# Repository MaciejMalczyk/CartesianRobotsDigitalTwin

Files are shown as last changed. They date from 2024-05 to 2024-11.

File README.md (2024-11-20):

# Cartesian Robots Digital Twin

Master's degree project. Functional pair of robots with digital twin made in FreeCAD. Repository consist all elements to build robots, program controllers and run software.

<p align="center">
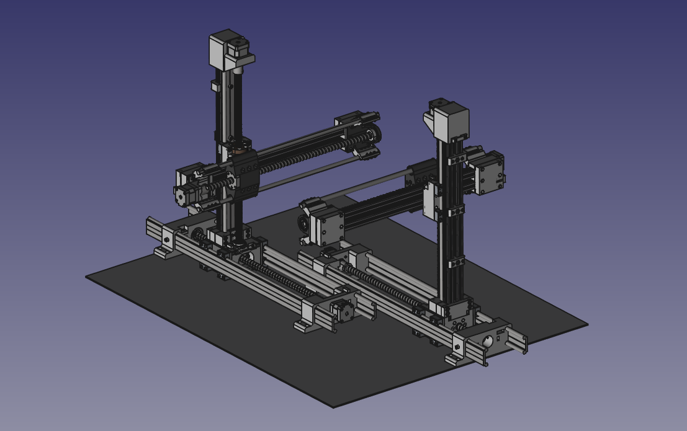
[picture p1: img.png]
    
</p>

## Contents

1. digitalTwin - FreeCAD project containing simplified models of robots with calculations,
2. documentation - 2D documentation of robots,
3. electronics - electronics schematic with designed board in KiCAD; used to connect motors with Arduino,
4. model - Autodesk Inventor model with .step export; additional FreeCAD designed t-slot nuts.
5. software - Arduino Uno code; FreeCAD macro for digitalTwin; misc - udev rules, examples; Qt ui.

## License

SOFTWARE: MIT
HARDWARE: CERN OHL v2, unless specified below

Igus® parts:
https://www.igus.eu/info/company-terms-and-conditions-de#section_15

Item® parts:
https://pl.item24.com/en/terms-and-conditions/

Autodesk Inventor Content Center files can have their own license.

## Acknowledgments

People involved in pre-alpha versions of CAD model: Wojciech Pyka, Maksymilian Jędrzejowski, Mateusz Chudy, Witold Krafczyk, Olaf Tokarczyk.

Maksymilian Jędrzejowski:
https://omega.polsl.pl/info/author/PSLde2ebd91c94b4b639f68adfb76bbbfe9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

Witold Krafczyk:
https://omega.polsl.pl/info/author/PSL3ab3095431ce463fbf17f6ad56f56e03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

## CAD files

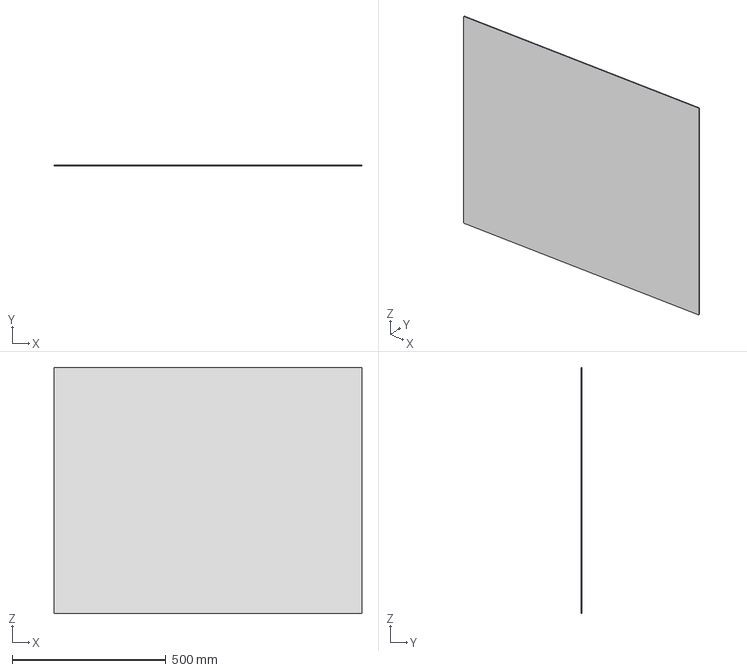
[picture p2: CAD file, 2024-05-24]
digitalTwin/aluminiumBase_ipt/0005.step
1000.0 x 3.00 x 800.0 mm

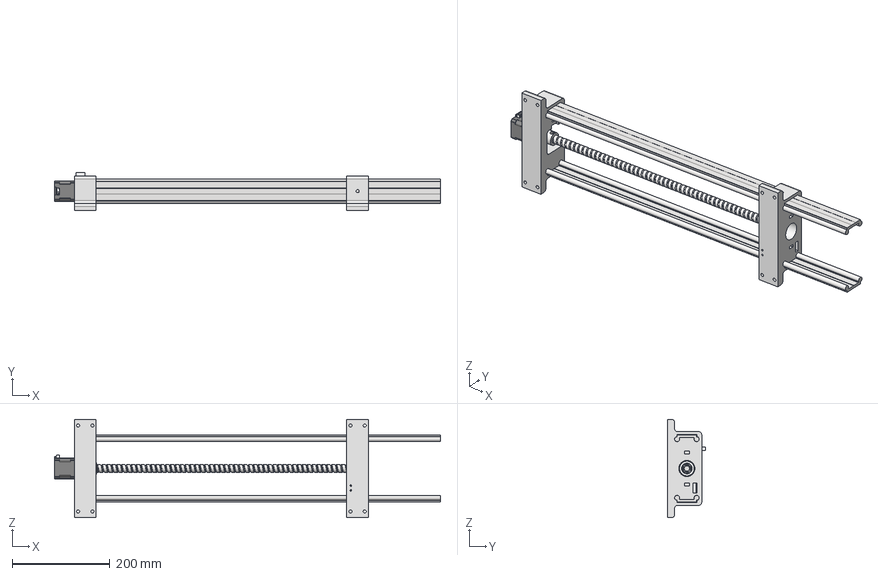
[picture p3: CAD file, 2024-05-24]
digitalTwin/X.stp
790.5 x 78.5 x 201.0 mm
Y_motor_mount
WS_10_40_X x 2
Y_motor_mount_1
Nema17 Stepper Motor
Cartesian1_BallScrew
Cartesian2_BallBearing_25x37x7
Cartesian1_12_12_Clutch
X_end_floating_cup
Connector_female
Stop_sw

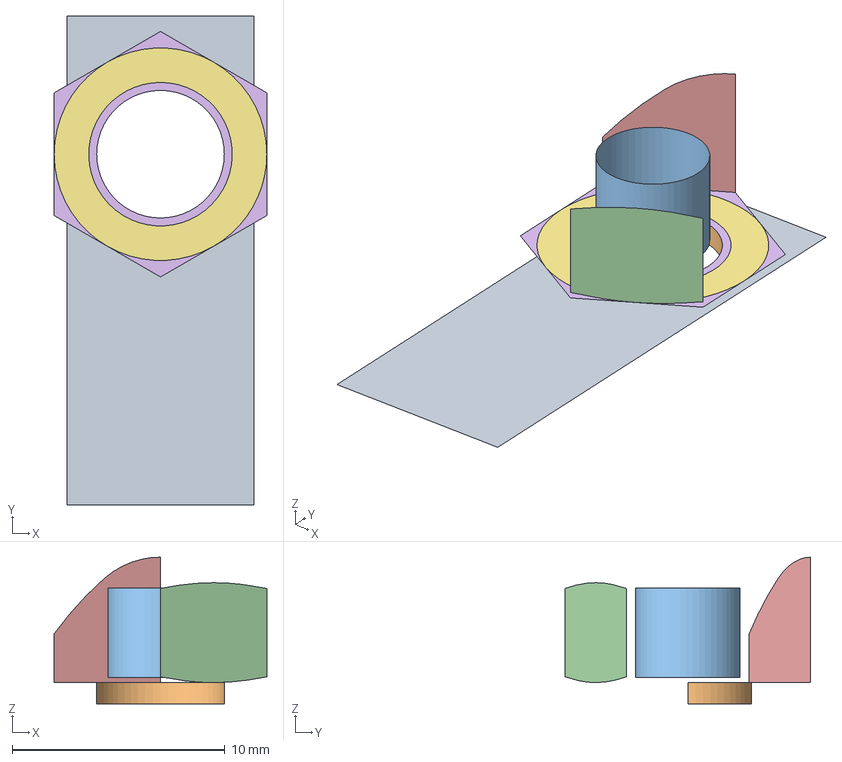
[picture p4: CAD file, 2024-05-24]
model/Additions/tslotNut8_M6.FCStd
10.0 x 23.0 x 6.90 mm
_Element
_Element001
_Element002
_Element003
_Element004
_Element005
_Element006

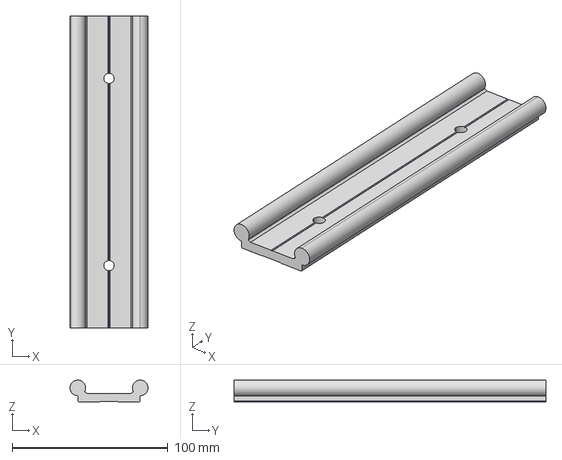
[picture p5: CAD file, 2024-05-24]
model/Workspaces/Obszar roboczy/content/igus/WS_10_40_200_1.stp
50.0 x 200.0 x 14.0 mm

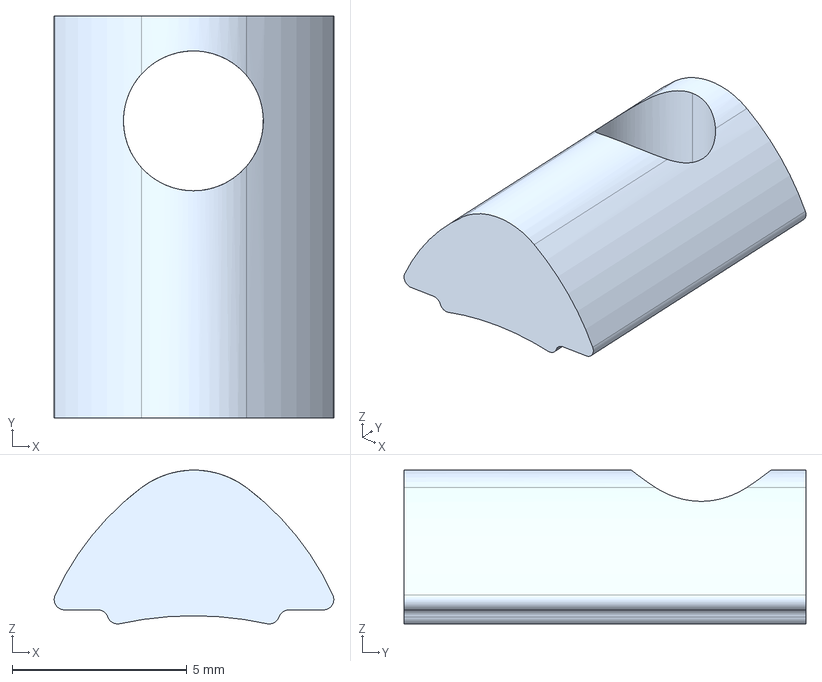
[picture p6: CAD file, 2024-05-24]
model/Workspaces/Obszar roboczy/content/item/item_0037006_Wpust_przesuwny_5_St_M4_1.stp
8.00 x 11.5 x 4.40 mm

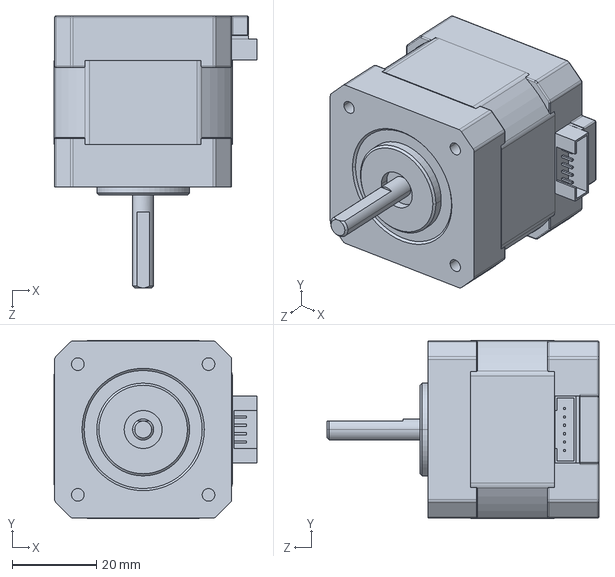
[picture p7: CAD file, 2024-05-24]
model/Workspaces/Obszar roboczy/content/nema17/17HS4401.STEP
48.2 x 42.3 x 64.5 mm

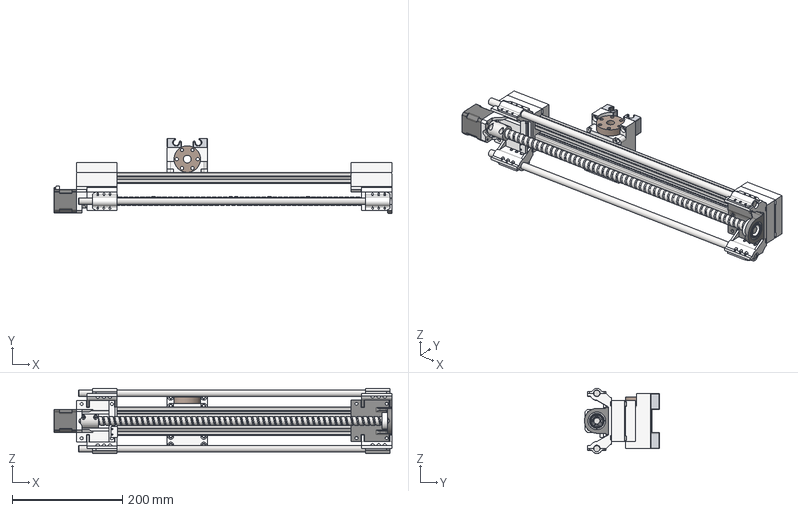
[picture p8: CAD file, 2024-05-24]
digitalTwin/Y.stp
612.5 x 136.2 x 118.5 mm
ZY_mount x 2
ZY_rod_mount x 2
motormount
Z_endstop_mount
Stop_sw
Z_bearingmount
item_0037003_Profile_5_20x20_L=564_1 x 2
Cartesian1_12mm_Rod x 2
Cartesian2_BallBearing_25x37x7
Cartesian1_X_RodCover x 4
Nema17 Stepper Motor
Cartesian1_12_12_Clutch
Cartesian1_BallScrew
Y_end_cover
Z_carriage
Cartesian1_Z_TrapezoiadlNut
WJ200UM_01_10_1 x 4
XItemEndCoverConnector
X_end_floating_cup

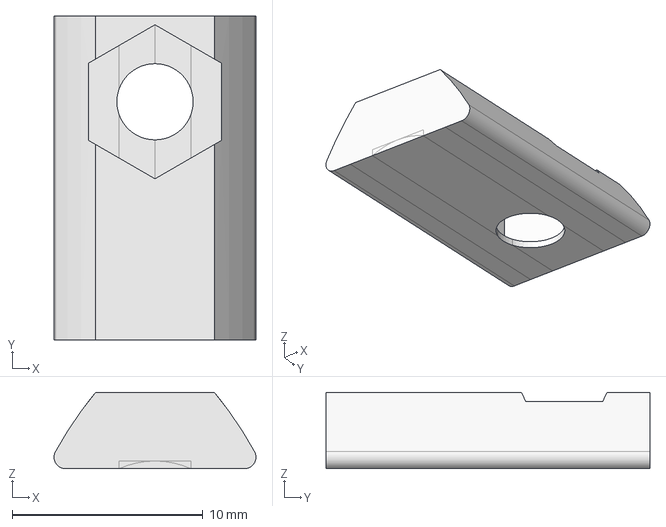
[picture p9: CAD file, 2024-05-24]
model/Additions/tslotNut6_M4.FCStd
10.6 x 17.0 x 4.00 mm

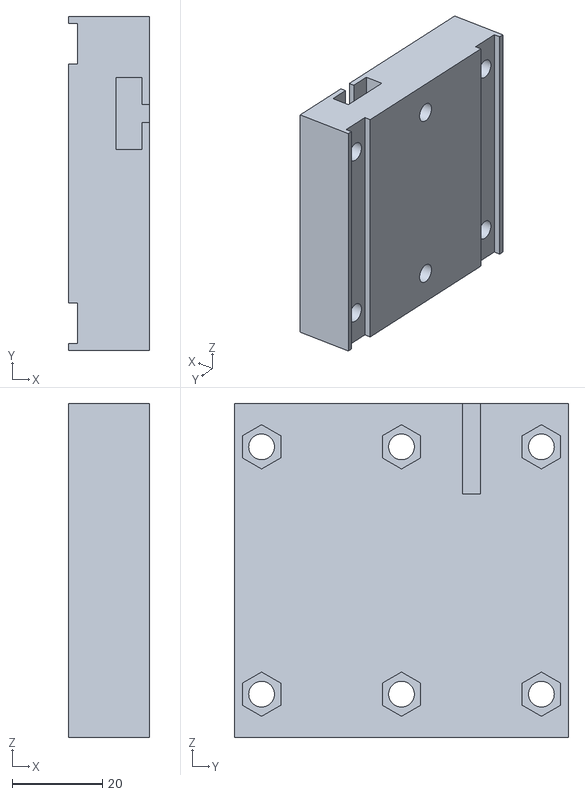
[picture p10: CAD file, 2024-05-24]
model/Workspaces/Obszar roboczy/assembly_v3/X/XItemEndCoverConnector.stl
18.0 x 74.0 x 74.0

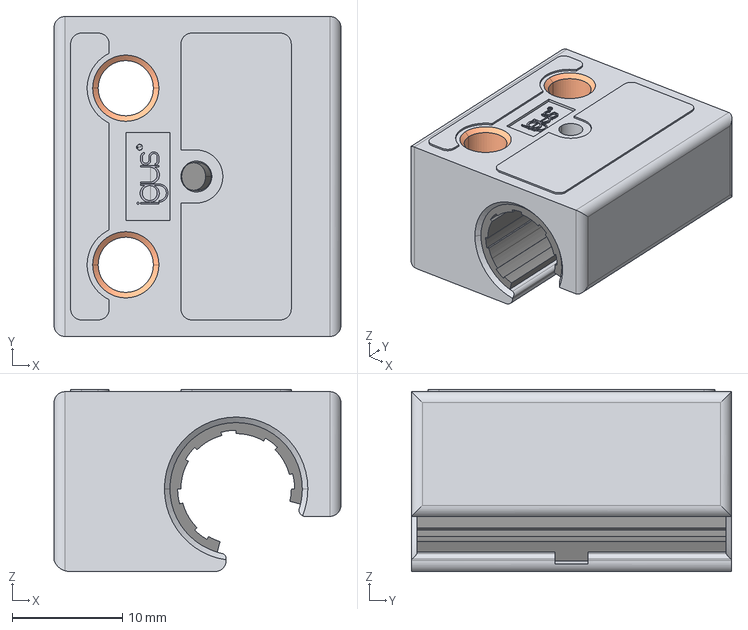
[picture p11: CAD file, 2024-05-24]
model/Workspaces/Obszar roboczy/content/igus/WJ200UM_01_10_1.stp
26.0 x 29.0 x 16.5 mm

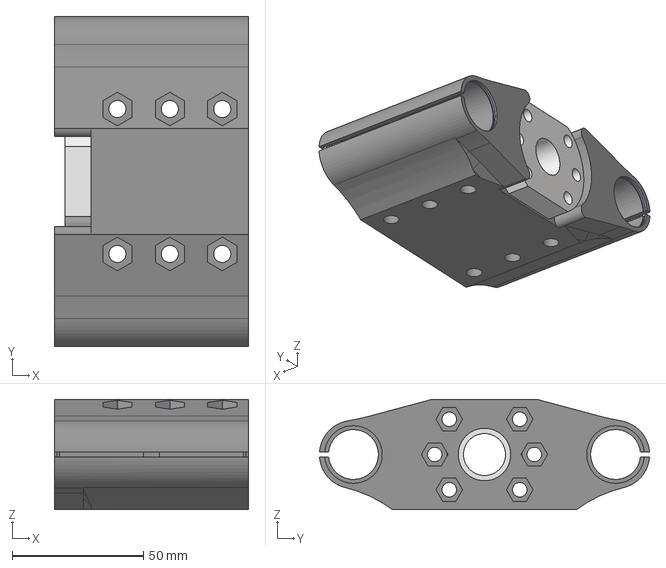
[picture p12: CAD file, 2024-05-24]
digitalTwin/C.stp
74.0 x 125.9 x 42.0 mm
Cartesian1_XYCarriage
Cartesian1_BallNut

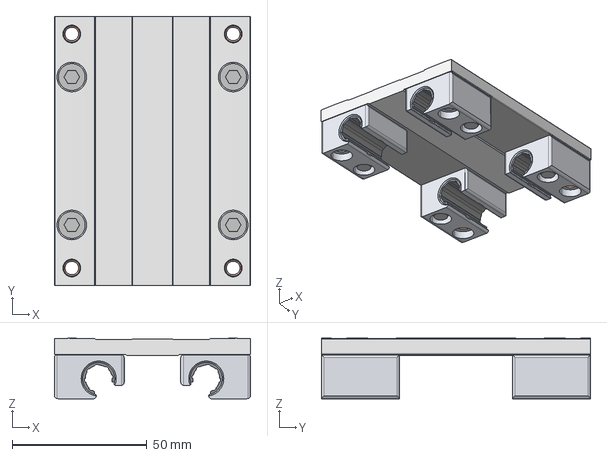
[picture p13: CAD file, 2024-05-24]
model/Workspaces/Obszar roboczy/content/igus/WW_10_40_10_2.stp
73.0 x 100.0 x 22.5 mm

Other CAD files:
model/Workspaces/Obszar roboczy/assembly_v3/Assembly.dwg
model/Workspaces/Obszar roboczy/assembly_v3/X/X.dwg
model/Workspaces/Obszar roboczy/assembly_v3/Y/Y.dwg
model/Workspaces/Obszar roboczy/assembly_v3/Z/Z.dwg
model/Workspaces/Obszar roboczy/content/igus/WS_10_80_200_1_FRONT.dwg
model/Workspaces/Obszar roboczy/assembly_v3/OldVersions/Assembly.0012.dwg
digitalTwin/aluminiumBase.ipt
model/Workspaces/Obszar roboczy/CC/pl-PL/ANSI B18.16.3M(2)/ANSI B18.16.3M - Klasa właściwości 5 i 10 - Metryczny M3 x 0.5 Typ metalowy.ipt
model/Workspaces/Obszar roboczy/CC/pl-PL/DIN 125-1 A/DIN 125 - A 3,2.ipt
model/Workspaces/Obszar roboczy/CC/pl-PL/DIN 472(1)/DIN 472 - 28 x 1,2.ipt
model/Workspaces/Obszar roboczy/CC/pl-PL/DIN 7984/DIN 7984 - M3 x 14.ipt
model/Workspaces/Obszar roboczy/CC/pl-PL/DIN 7984/DIN 7984 - M3 x 18.ipt
model/Workspaces/Obszar roboczy/CC/pl-PL/DIN 7984/DIN 7984 - M4 x 14.ipt
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

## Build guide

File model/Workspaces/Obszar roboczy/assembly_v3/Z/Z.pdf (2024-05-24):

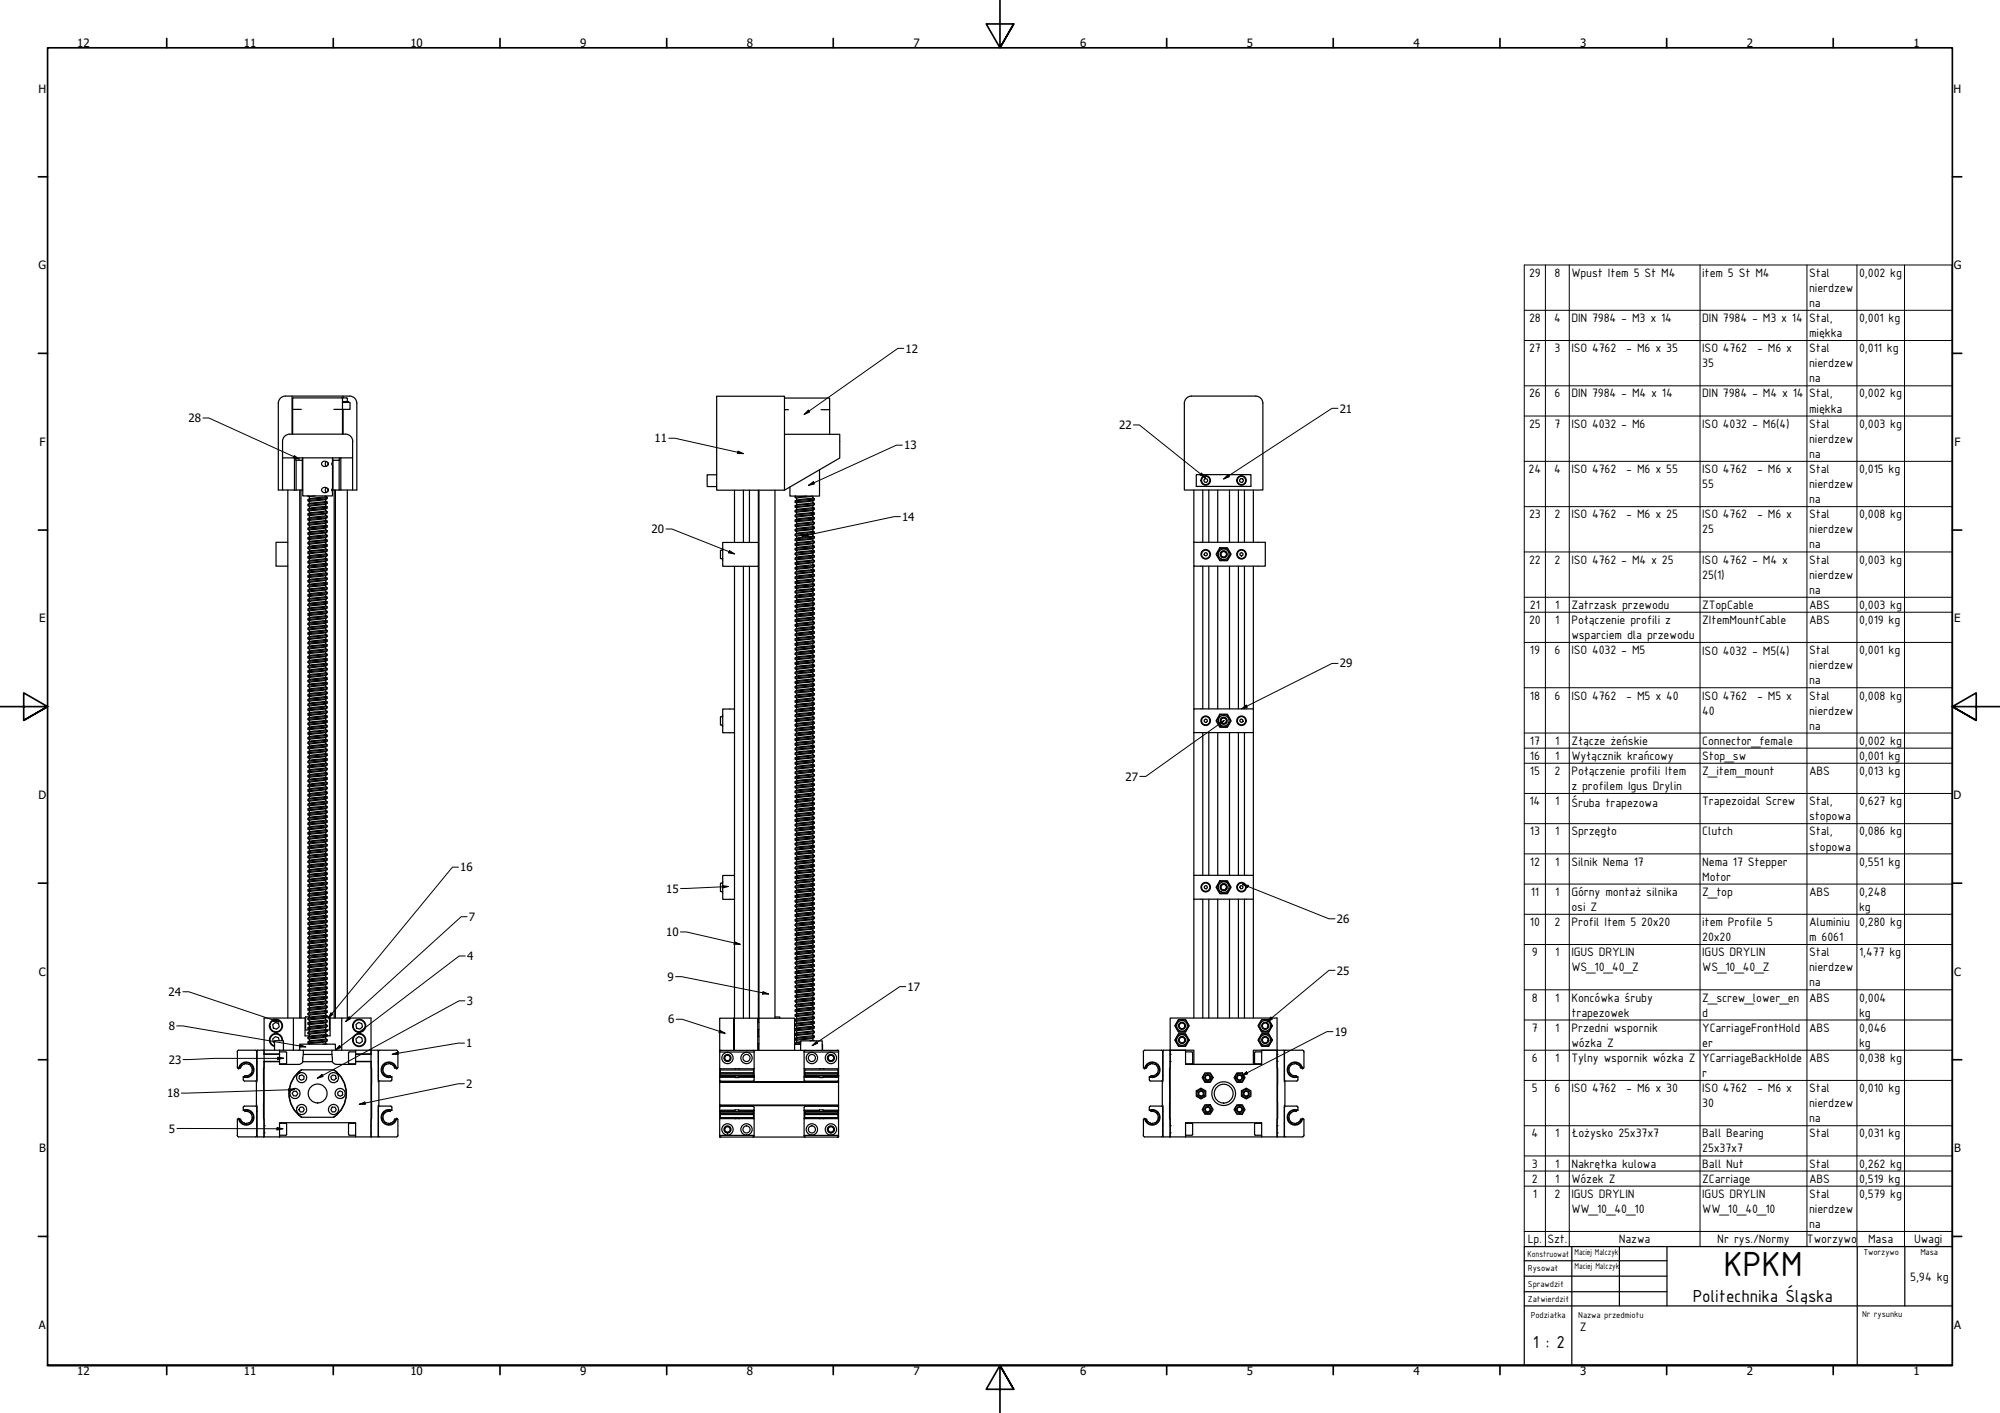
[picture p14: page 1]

2 9 | 8 | W p u s t It e m 5 S t M 4 | it e m 5 S t M 4 | S t a l nie r d z e w n a | 0,0 0 2 k g

2 8 | 4 | DIN 7 9 8 4 -M 3 x 1 4 | DIN 7 9 8 4 -M 3 x 1 4 | S t a l, mi k k a | 0,0 0 1 k g

2 7 | 3 | IS O 4 7 6 2 -M 6 x 3 5 | | S a ISO 4762 - M6 x 35 t a l nie r d z e w n | 0,0 1 1 k g

2 6 | 6 | DIN 7 9 8 4 -M 4 x 1 4 | DIN 7 9 8 4 -M 4 x 1 4 | S t a l, mi k k a | 0,0 0 2 k g

2 5 | 7 | IS O 4 0 3 2 -M 6 | ( ) IS O 4 0 3 2 -M 6 4 | S t a l nie r d z e w n a | 0,0 0 3 k g

2 4 | 4 | IS O 4 7 6 2 -M 6 x 5 5 | | S a ISO 4762 - M6 x 55 t a l nie r d z e w n | 0,0 1 5 k g

2 3 | 2 | IS O 4 7 6 2 -M 6 x 2 5 | | S a ISO 4762 - M6 x 25 t a l nie r d z e w n | 0,0 0 8 k g

2 2 | 2 | IS O 4 7 6 2 -M 4 x 2 5 | | S a ISO 4762 - M4 x 25(1) t a l nie r d z e w n | 0,0 0 3 k g

2 1 | 1 | Z a t r z a s k p r z e w o d u | Z T o p C a b l e | A B S | 0,0 0 3 k g
2 0 | 1 |  P o ò c z e nie p r o fili z w s p a r cie m d l a p r z e w o d u | ZIt e m M o u n t C a b l e | A B S | 0,0 1 9 k g

1 9 | 6 | IS O 4 0 3 2 -M 5 | ( ) IS O 4 0 3 2 -M 5 4 | S t a l nie r d z e w n a | 0,0 0 1 k g

1 8 | 6 | IS O 4 7 6 2 -M 5 x 4 0 | | S a ISO 4762 - M5 x 40 t a l nie r d z e w n | 0,0 0 8 k g

1 7 | 1 |  Z  ò c z e  e s kie | C o n n e c t o r_f e m a l e | | 0,0 0 2 k g
1 6 | 1 |  W y  ò c z nik k r a c o w y | S t o p_s w | | 0,0 0 1 k g
1 5 | 2 |  P o ò c z e nie p r o fili It e m z p r o fil e m Ig u s D r y lin | Z_it e m_m o u n t | A B S | 0,0 1 3 k g

1 4 | 1 |  r u b a t r a p e z o w a | T r a p e z oid a l S c r e w | S t a l, s t o p o w a | 0,6 2 7 k g

1 2 | 1 | Sil nik N e m a 1 7 | N e m a 1 7 S t e p p e r M o t o r | | 0,5 5 1 k g

1 1 | 1 | ¦ G r n y m o n t a  sil nik a o si Z | Z_t o p | A B S | 0,2 4 8 k g

1 0 | 2 | P r o fil It e m 5 2 0 x 2 0 | | A l u miniu 1 item Profile 5 20x20 m 6 0 6 | 0,2 8 0 k g

9 | 1 | | | S a IGUS DRYLIN WS_10_40_Z IGUS DRYLIN WS_10_40_Z t a l nie r d z e w n | 1,4 7 7 k g

7 | 1 | P r z e d ni w s p o r nik w ¦ z k a Z | Y C a r ria g e F r o n t H o l d e r | A B S | 0,0 4 6 k g

6 | 1 | ¦ T y l n y w s p o r nik w z k a Z | Y C a r ria g e B a c k H o l d e r | A B S | 0,0 3 8 k g

5 | 6 | IS O 4 7 6 2 -M 6 x 3 0 | | S a ISO 4762 - M6 x 30 t a l nie r d z e w n | 0,0 1 0 k g

4 | 1 |  o  y s k o 2 5 x 3 7 x 7 | B a l l B e a rin g 2 5 x 3 7 x 7 | S t a l | 0,0 3 1 k g

3 | 1 | N a k r  t k a k u l o w a | B a l l N u t | S t a l | 0,2 6 2 k g
2 | 1 | ¦ W z e k Z | Z C a r ria g e | A B S | 0,5 1 9 k g
1 | 2 | | | S a IGUS DRYLIN WW_10_40_10 IGUS DRYLIN WW_10_40_10 t a l nie r d z e w n | 0,5 7 9 k g
K o n s t r u o w a  | M a ciej M a l c z y k | | K P K M  P o lit e c h nik a l ò s k a | T w o r z y w o | M a s a 5,9 4 k g
 R y s o w a | M a ciej M a l c z y k

Z a t wie r d zi

P o d zia  k a 1 : 2 | N a z w a p r z e d mio t u Z | | | N r r y s u n k u

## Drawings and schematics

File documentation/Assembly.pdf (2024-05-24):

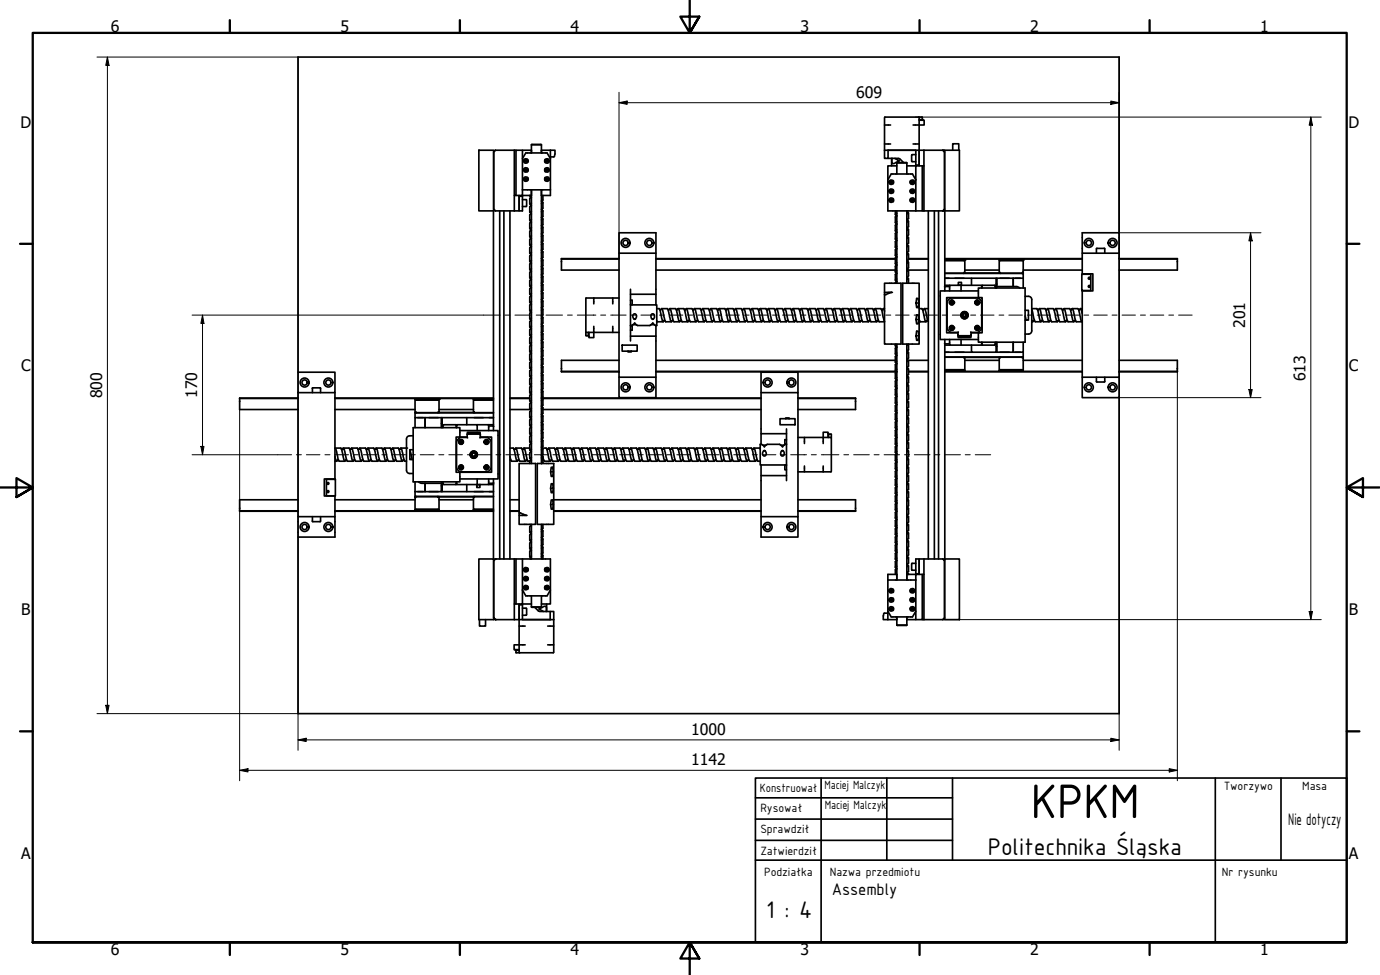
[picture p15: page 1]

Konstruowa | Maciej Malczyk | KPKM Politechnika lòska | Tworzywo | Masa Nie dotyczy
Rysowa | Maciej Malczyk
Zatwierdzi

Sprawdzi

Podziaka 1 : 4 | Nazwa przedmiotu Assembly | | Nr rysunku

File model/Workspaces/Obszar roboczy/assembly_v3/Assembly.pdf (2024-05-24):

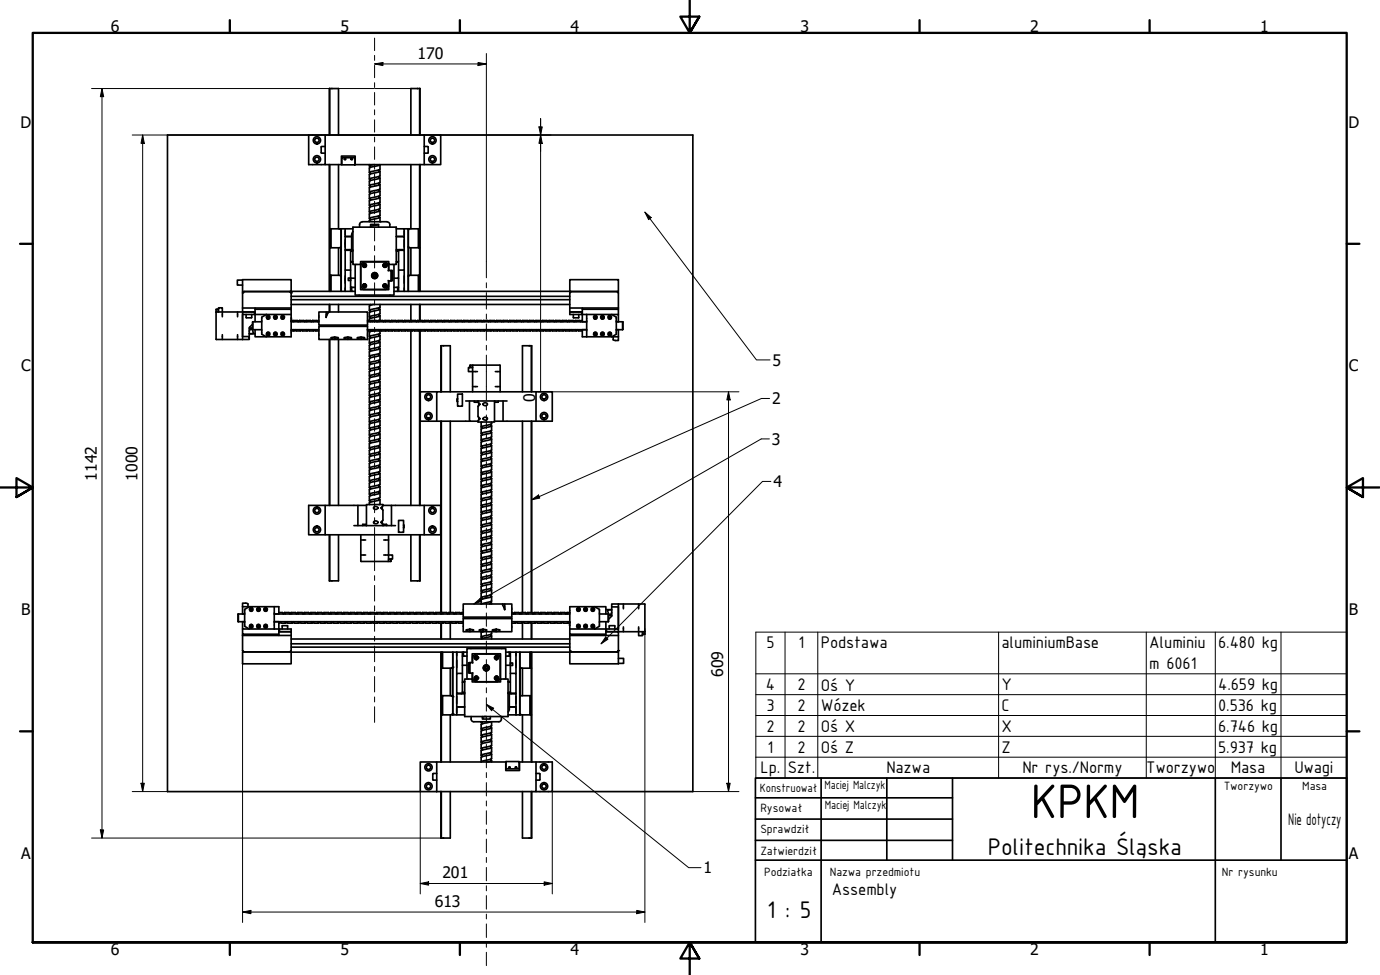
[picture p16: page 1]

5 | 1 | Podstawa | aluminiumBase | Aluminiu m 6061 | 6.480 kg

4 | 2 | O Y | Y | | 4.659 kg
3 | 2 | W¦zek | C | | 0.536 kg
2 | 2 | O X | X | | 6.746 kg
1 | 2 | O Z | Z | | 5.937 kg
Lp. | Szt. | Nazwa | Nr rys./Normy | Tworzywo | Masa | Uwagi
Konstruowa | Maciej Malczyk | | KPKM Politechnika lòska | Tworzywo | Masa Nie dotyczy
Rysowa | Maciej Malczyk
Zatwierdzi

Sprawdzi

Podziaka 1 : 5 | Nazwa przedmiotu Assembly | | | Nr rysunku

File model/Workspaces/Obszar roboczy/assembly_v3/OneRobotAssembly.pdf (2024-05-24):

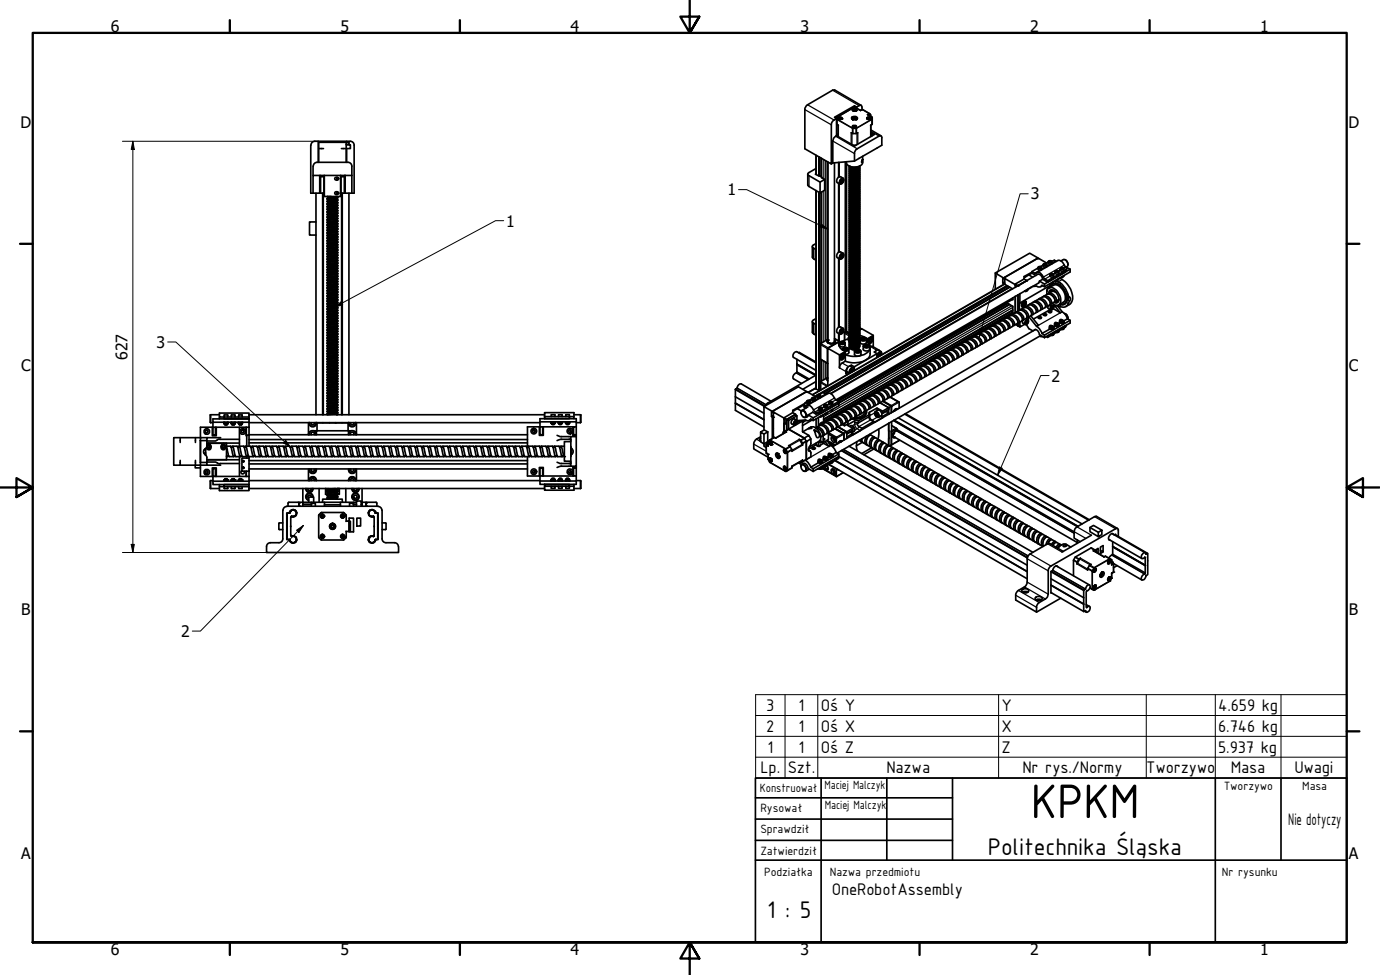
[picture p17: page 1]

3 | 1 | O Y | Y | | 4.659 kg
2 | 1 | O X | X | | 6.746 kg
1 | 1 | O Z | Z | | 5.937 kg
Lp. | Szt. | Nazwa | Nr rys./Normy | Tworzywo | Masa | Uwagi
Konstruowa | Maciej Malczyk | | KPKM Politechnika lòska | Tworzywo | Masa Nie dotyczy
Rysowa | Maciej Malczyk
Zatwierdzi

Sprawdzi

Podziaka 1 : 5 | Nazwa przedmiotu OneRobotAssembly | | | Nr rysunku

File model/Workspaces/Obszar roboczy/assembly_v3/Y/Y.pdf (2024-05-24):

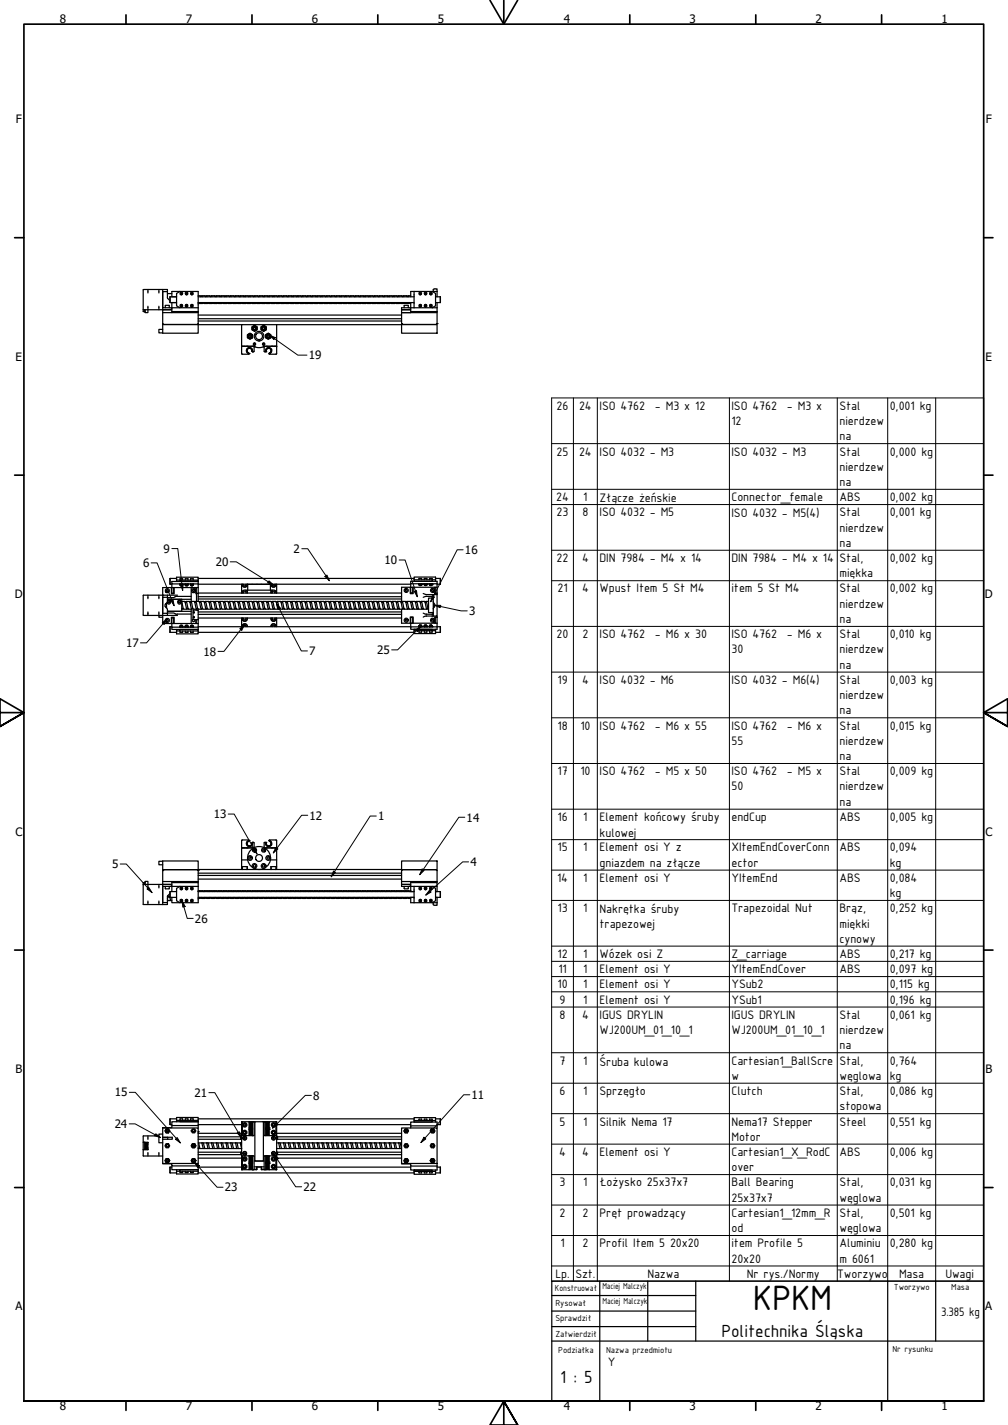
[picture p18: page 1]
Stal,; Ball Bearing

26 | 24 | ISO 4762 - M3 x 12 | ISO 4762 - M3 x 12 | Stal nierdzew na | 0,001 kg

25 | 24 | ISO 4032 - M3 | ISO 4032 - M3 | Stal nierdzew na | 0,000 kg

24 | 1 | Zòcze eskie | Connector_female | ABS | 0,002 kg
23 | 8 | ISO 4032 - M5 | ISO 4032 - M5(4) | Stal nierdzew na | 0,001 kg

22 | 4 | DIN 7984 - M4 x 14 | DIN 7984 - M4 x 14 | Stal, mikka | 0,002 kg

21 | 4 | Wpust Item 5 St M4 | item 5 St M4 | Stal nierdzew na | 0,002 kg

20 | 2 | ISO 4762 - M6 x 30 | ISO 4762 - M6 x 30 | Stal nierdzew na | 0,010 kg

19 | 4 | ISO 4032 - M6 | ISO 4032 - M6(4) | Stal nierdzew na | 0,003 kg

18 | 10 | ISO 4762 - M6 x 55 | ISO 4762 - M6 x 55 | Stal nierdzew na | 0,015 kg

17 | 10 | ISO 4762 - M5 x 50 | ISO 4762 - M5 x 50 | Stal nierdzew na | 0,009 kg

16 | 1 | Element kocowy ruby kulowej | endCup | ABS | 0,005 kg

15 | 1 | Element osi Y z gniazdem na zòcze | XItemEndCoverConn ector | ABS | 0,094 kg

14 | 1 | Element osi Y | YItemEnd | ABS | 0,084 kg

13 | 1 | Nakrtka ruby trapezowej | Trapezoidal Nut | Bròz, mikki cynowy | 0,252 kg

12 | 1 | W¦zek osi Z | Z_carriage | ABS | 0,217 kg
11 | 1 | Element osi Y | YItemEndCover | ABS | 0,097 kg
10 | 1 | Element osi Y | YSub2 | | 0,115 kg
9 | 1 | Element osi Y | YSub1 | | 0,196 kg
8 | 4 | IGUS DRYLIN WJ200UM_01_10_1 | IGUS DRYLIN WJ200UM_01_10_1 | Stal nierdzew na | 0,061 kg

7 | 1 | ruba kulowa | Cartesian1_BallScre w | Stal, wglowa | 0,764 kg

6 | 1 | Sprzgo | Clutch | Stal, stopowa | 0,086 kg

5 | 1 | Silnik Nema 17 | Nema17 Stepper Motor | Steel | 0,551 kg

4 | 4 | Element osi Y | Cartesian1_X_RodC over | ABS | 0,006 kg

2 | 2 | Prt prowadzòcy | Cartesian1_12mm_R od | Stal, wglowa | 0,501 kg

1 | 2 | Profil Item 5 20x20 | item Profile 5 20x20 | Aluminiu m 6061 | 0,280 kg
Konstruowa | Maciej Malczyk | | KPKM Politechnika lòska | Tworzywo | Masa 3.385 kg
Rysowa | Maciej Malczyk
Zatwierdzi

Lp. | Szt. | Nazwa | Nr rys./Normy | Tworzywo | Masa | Uwagi

Sprawdzi

Podziaka 1 : 5 | Nazwa przedmiotu Y | | | Nr rysunku

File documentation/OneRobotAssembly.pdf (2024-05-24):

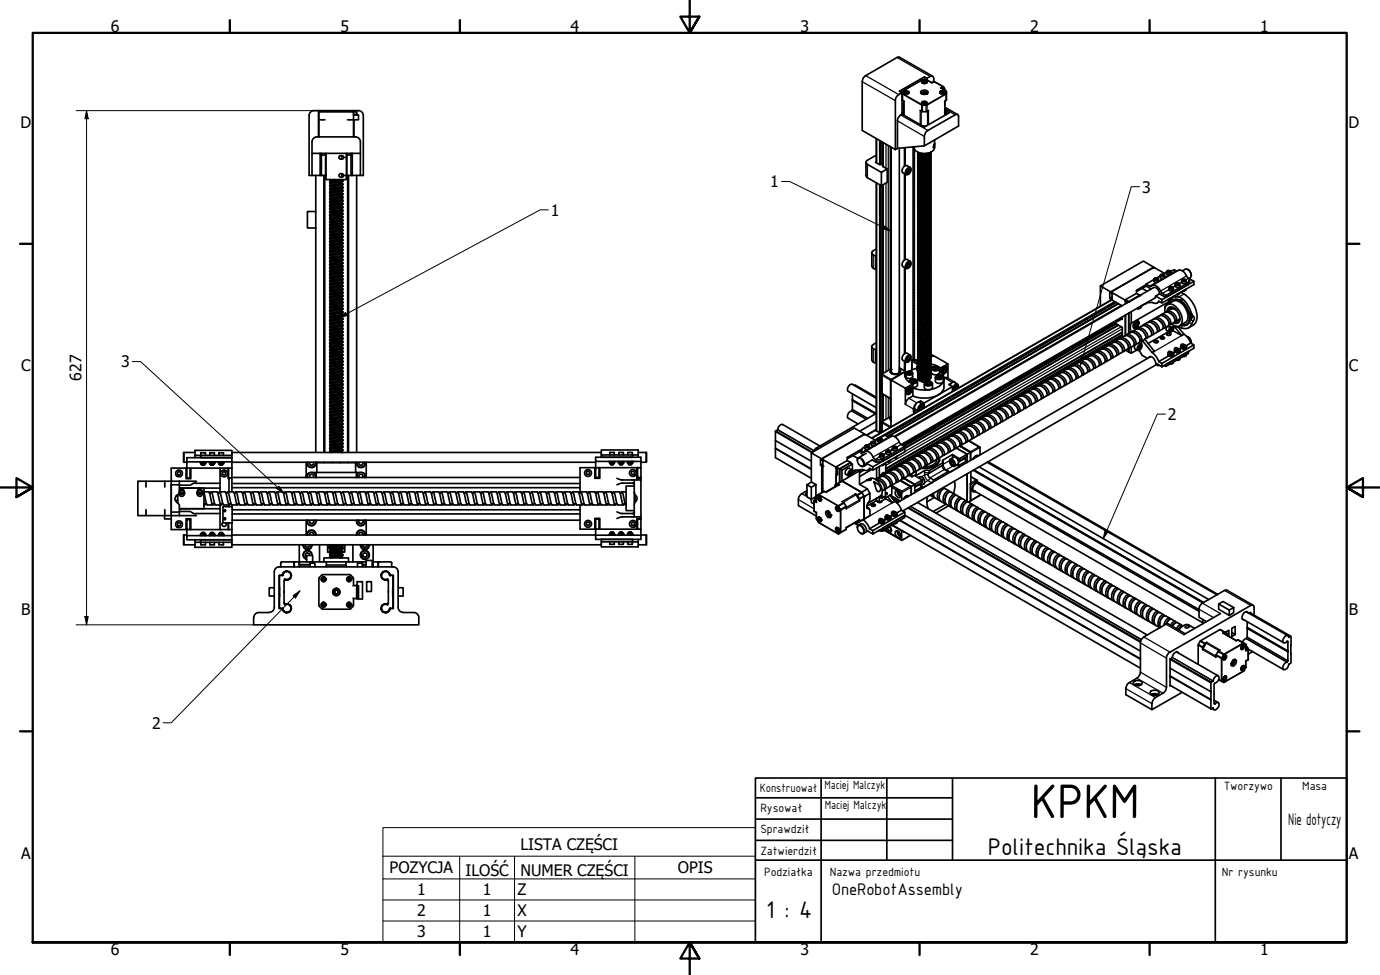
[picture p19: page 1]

Konstruowa | Maciej Malczyk | KPKM Politechnika lòska | Tworzywo | Masa Nie dotyczy
Rysowa | Maciej Malczyk
Zatwierdzi

Sprawdzi

LISTA CZCI

POZYCJA | ILOû | NUMER CZCI | OPIS

Podziaka 1 : 4 | Nazwa przedmiotu OneRobotAssembly | | Nr rysunku

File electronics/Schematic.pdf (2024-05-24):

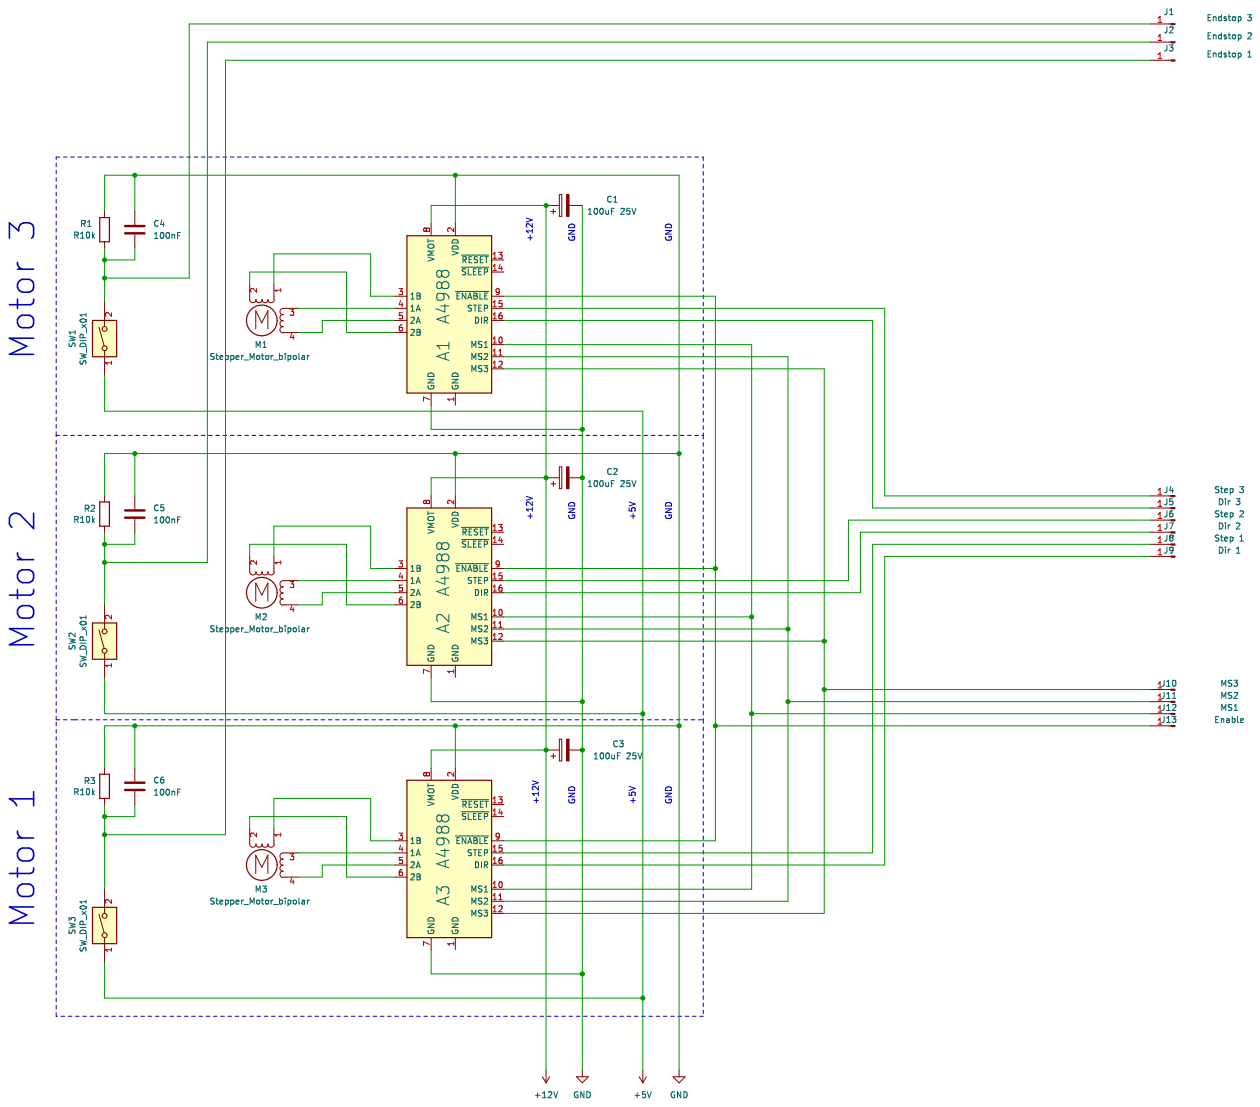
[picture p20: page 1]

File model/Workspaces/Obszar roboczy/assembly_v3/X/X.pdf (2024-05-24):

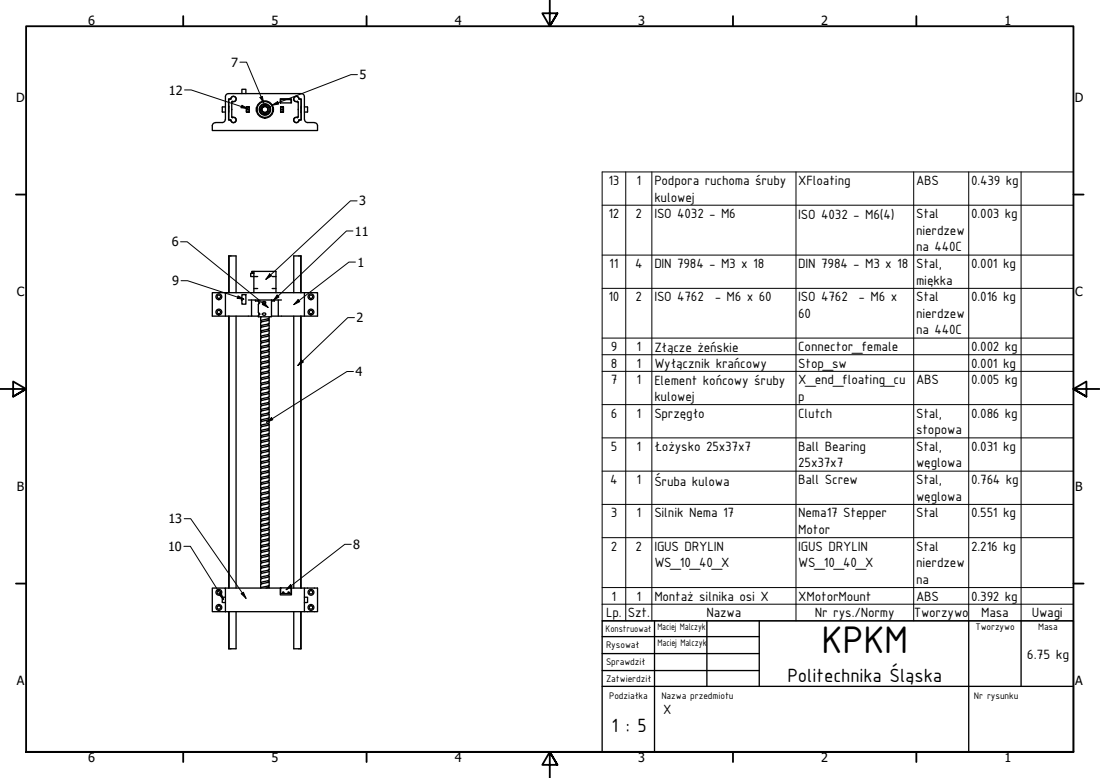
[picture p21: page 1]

1 3 | 1 | P o d p o r a r u c h o m a  r u b y k u l o w ej | X F l o a tin g | A B S | 0.4 3 9 k g

1 2 | 2 | IS O 4 0 3 2 -M 6 | IS O 4 0 3 2 -M 6 ( 4 ) | S t a l nie r d z e w n a 4 4 0 C | 0.0 0 3 k g

1 1 | 4 | DIN 7 9 8 4 -M 3 x 1 8 | DIN 7 9 8 4 -M 3 x 1 8 | S t a l, mi k k a | 0.0 0 1 k g

1 0 | 2 | IS O 4 7 6 2 -M 6 x 6 0 | | S t a l C ISO 4762 - M6 x 60 nie r d z e w n a 4 4 0 | 0.0 1 6 k g

9 | 1 | Z  ò c z e  e  s kie | C o n n e c t o r_f e m a l e | | 0.0 0 2 k g
8 | 1 | W y  ò c z nik k r a  c o w y | S t o p_s w | | 0.0 0 1 k g
7 | 1 | E l e m e n t k o  c o w y  r u b y k u l o w ej | X_e n d_f l o a tin g_c u p | A B S | 0.0 0 5 k g

5 | 1 |  o  y s k o 2 5 x 3 7 x 7 | B a l l B e a rin g 2 5 x 3 7 x 7 | S t a l, w  g l o w a | 0.0 3 1 k g

3 | 1 | Sil nik N e m a 1 7 | N e m a 1 7 S t e p p e r M o t o r | S t a l | 0.5 5 1 k g

2 | 2 | | | S a IGUS DRYLIN WS_10_40_X IGUS DRYLIN WS_10_40_X t a l nie r d z e w n | 2.2 1 6 k g

1 | 1 | M o n t a  sil nik a o si X | X M o t o r M o u n t | A B S | 0.3 9 2 k g
L p. S | z t. N | a z w a | N r r y s./ N o r m y | T w o r z y w o | M a s a | U w a
K o n s t r u o w a  | M a ciej M a l c z y k | | K P K M  P o lit e c h nik a l ò s k a | T w o r z y w o | M a s a 6.7 5 k g
R y s o w a  | M a ciej M a l c z y k

Z a t wie r d zi

P o d zia  k a 1 : 5 | N a z w a p r z e d mio t u X | | | N r r y s u n k u

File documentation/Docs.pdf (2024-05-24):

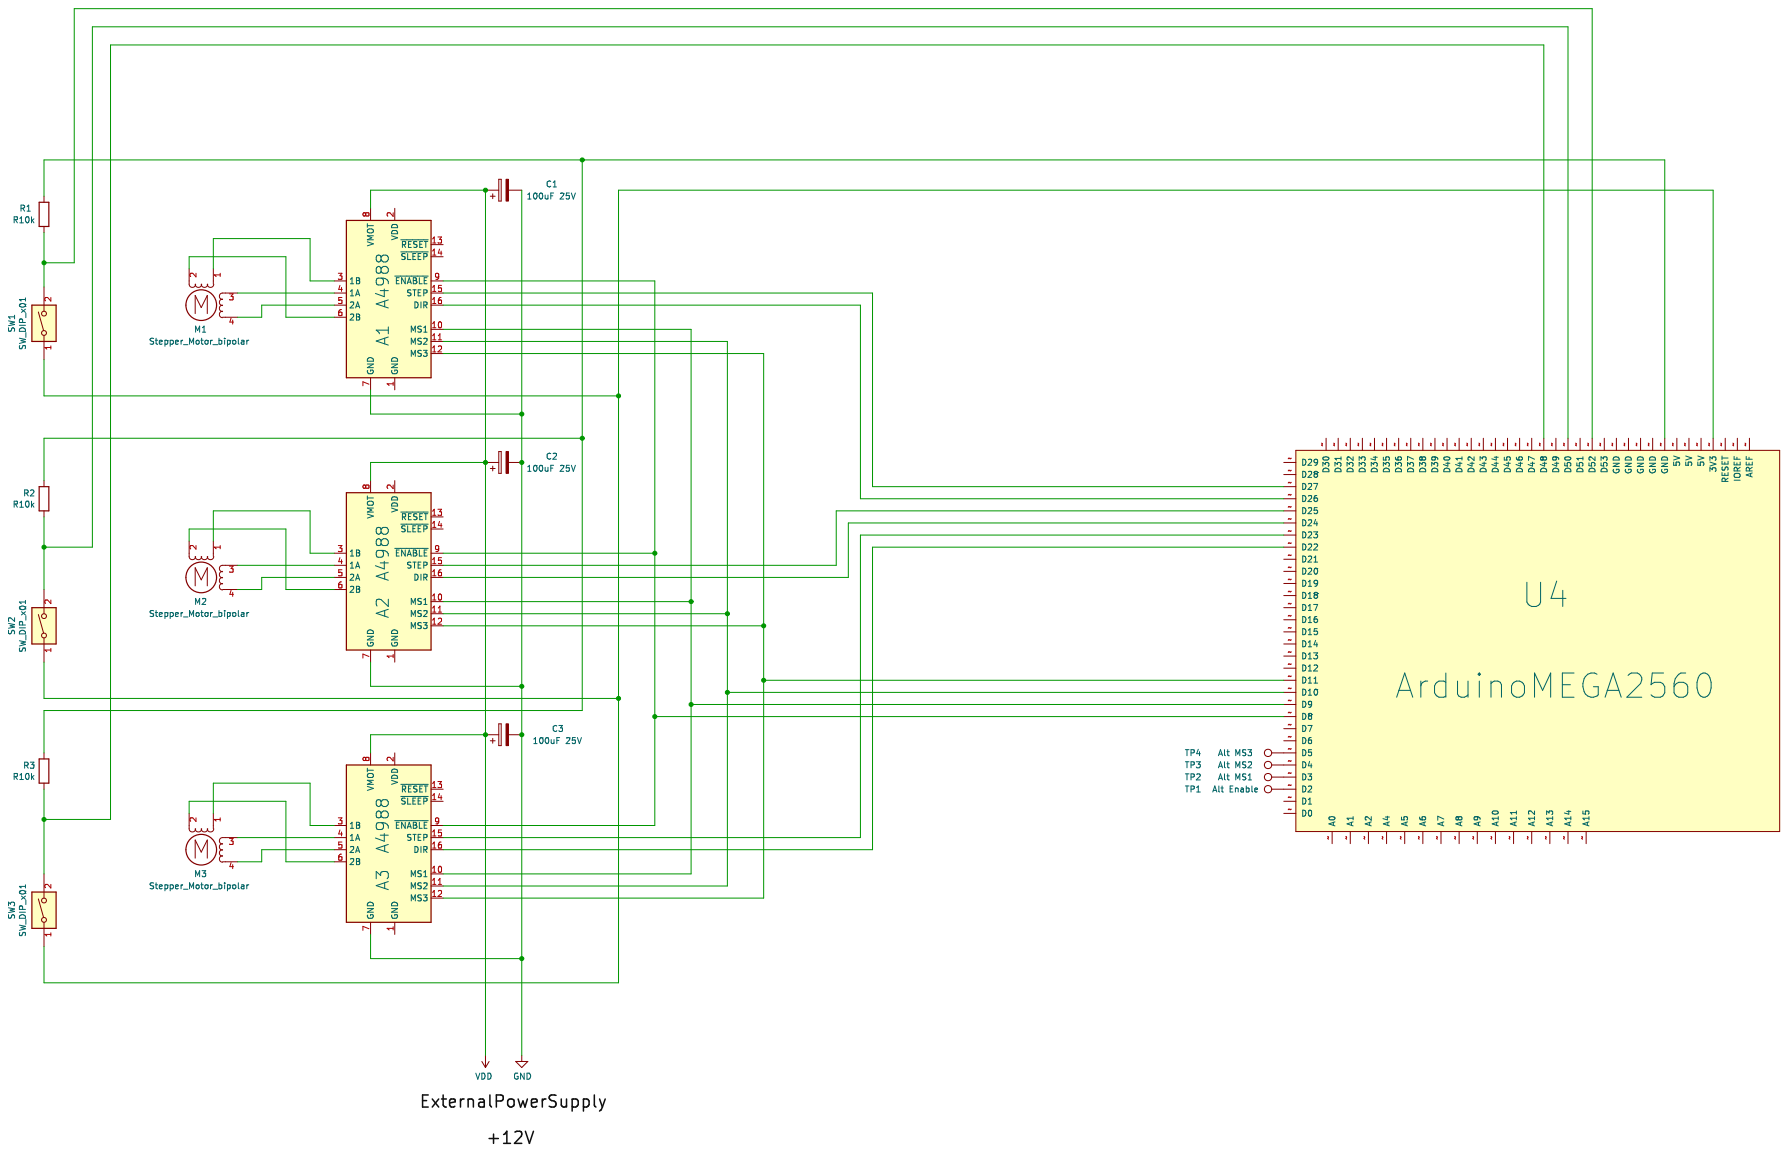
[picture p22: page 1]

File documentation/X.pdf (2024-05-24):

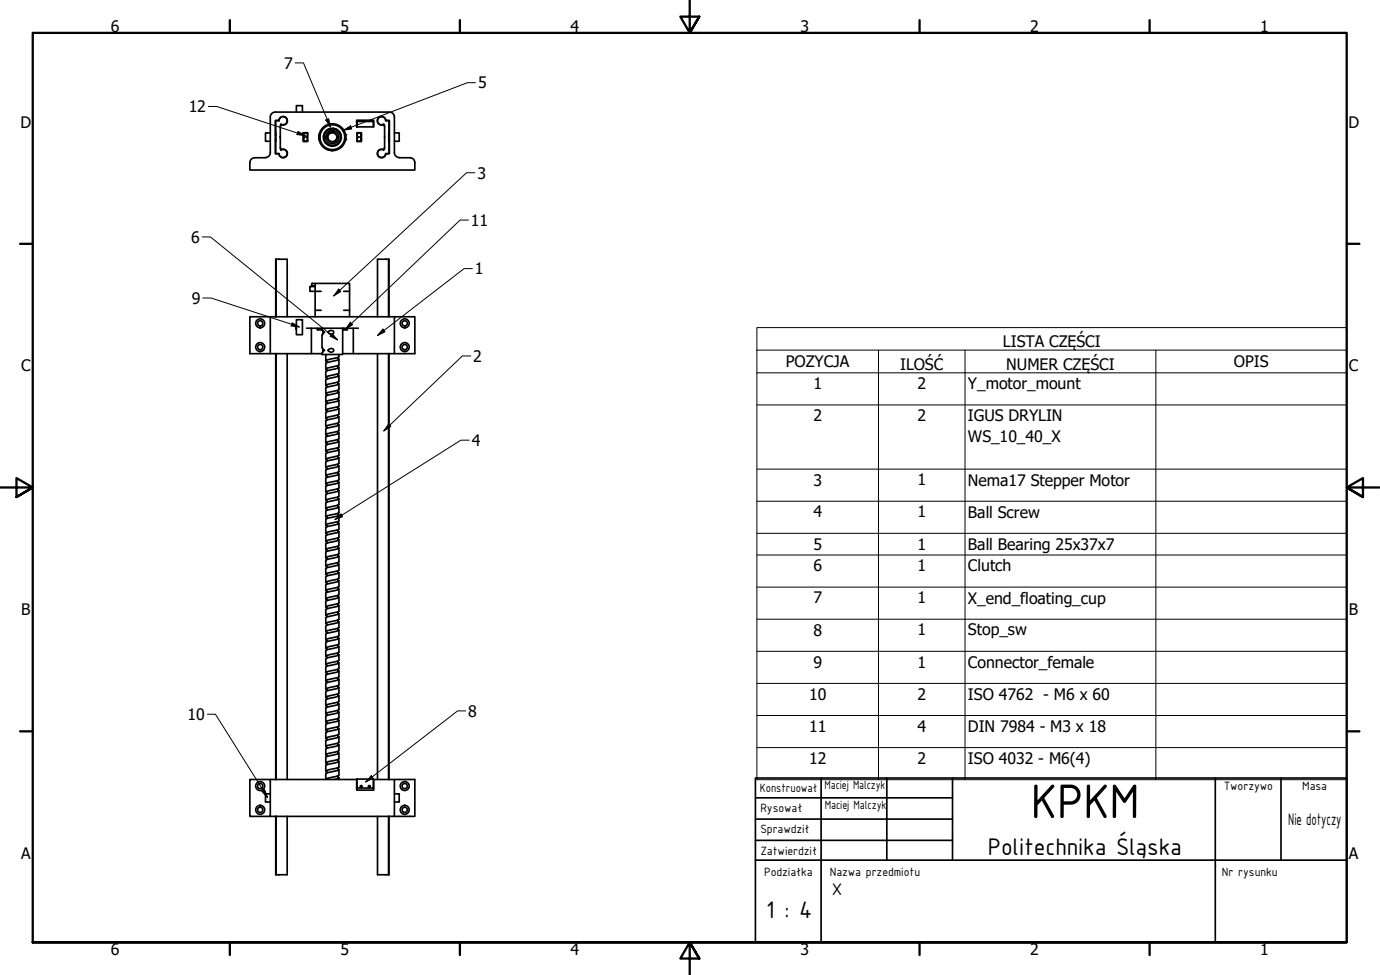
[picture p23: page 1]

P O Z Y C J A |  û I L O |  N U M E R C Z  C I | O P I S
1 | 2 | Y_ m o t o r_ m o u n t

4 | 1 | B all S c r e w

5 | 1 | B all B e a r i n g 2 5 x 3 7 x 7
6 | 1 | Clu t c h

7 | 1 | X_ e n d _flo a t i n g _ c u p

9 | 1 | C o n n e c t o r_ fe m ale

1 1 | 4 | D I N 7 9 8 4 -M 3 x 1 8
K o n s t r u o w a  | M a ciej M a l c z y k | | K P K M  P o lit e c h nik a l ò s k a | T w o r z y w o | M a s a Nie d o t y c z y
R y s o w a  | M a ciej M a l c z y k

Z a t wie r d zi

P o d zia  k a 1 : 4 | N a z w a p r z e d mio t u X | | | N r r y s u n k u

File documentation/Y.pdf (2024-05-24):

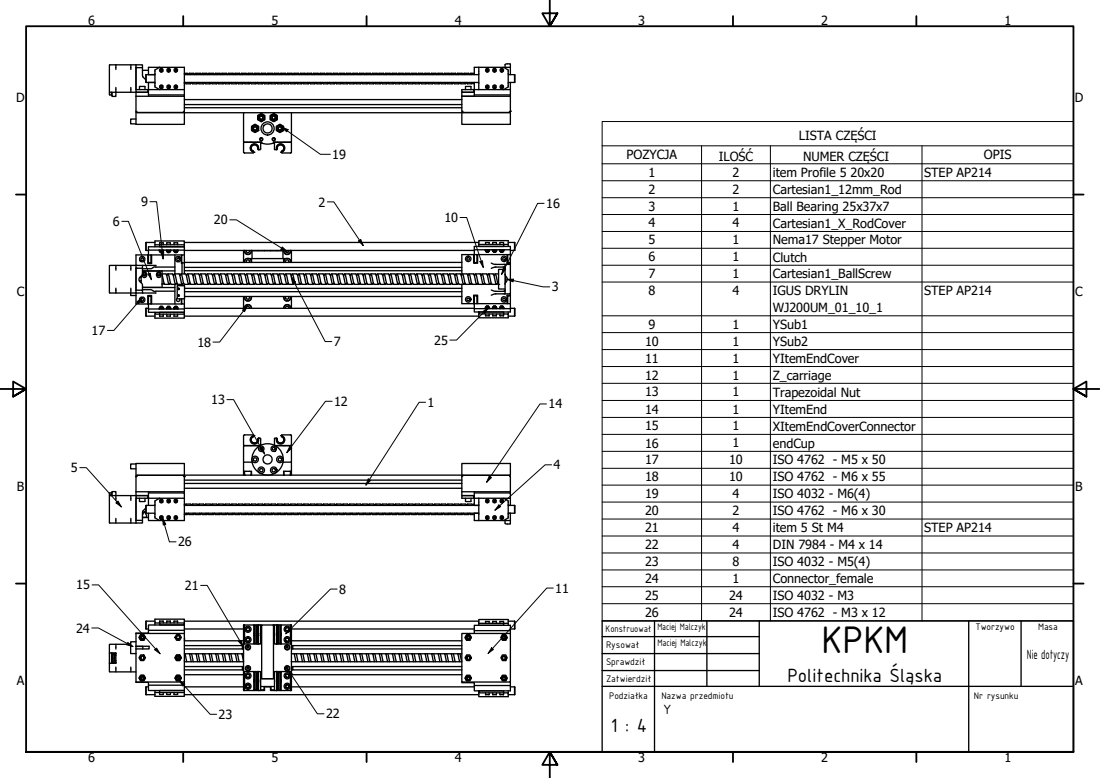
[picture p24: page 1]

P O Z Y C J A |  û I L O |  N U M E R C Z  C I | O P I S
1 | 2 | i t e m P r o f ile 5 2 0 x 2 0 | S T E P A P 2 1 4
2 | 2 | C a r t e s i a n 1 _ 1 2 m m _ R o d
3 | 1 | B all B e a r i n g 2 5 x 3 7 x 7
4 | 4 | C a r t e s i a n 1 _X_ R o d C o v e r
5 | 1 | N e m a 1 7 S t e p p e r M o t o r
6 | 1 | Clu t c h
7 | 1 | C a r t e s i a n 1 _ B allS c r e w
8 | 4 | I G U S D RY L I N W J 2 0 0 U M _ 0 1 _ 1 0 _ 1 | S T E P A P 2 1 4

1 0 | 1 | Y S u b 2
1 1 | 1 | Y I t e m E n d C o v e r
1 2 | 1 | Z _ c a r r i a g e
1 3 | 1 | T r a p e z o i d al N u t
1 4 | 1 | Y I t e m E n d
1 5 | 1 | X I t e m E n d C o v e r C o n n e c t o r
1 6 | 1 | e n d C u p
1 7 | 1 0 | I S O 4 7 6 2 -M 5 x 5 0
1 8 | 1 0 | I S O 4 7 6 2 -M 6 x 5 5
1 9 | 4 | I S O 4 0 3 2 -M 6 ( 4 )
2 0 | 2 | I S O 4 7 6 2 -M 6 x 3 0
2 1 | 4 | i t e m 5 S t M 4 | S T E P A P 2 1 4
2 2 | 4 | D I N 7 9 8 4 -M 4 x 1 4
2 3 | 8 | I S O 4 0 3 2 -M 5 ( 4 )
2 4 | 1 | C o n n e c t o r_ fe m ale
2 5 | 2 4 | I S O 4 0 3 2 -M 3
2 6 | 2 4 | I S O 4 7 6 2 -M 3 x 1 2
K o n s t r u o w a  | M a ciej M a l c z y k | | K P K M  P o lit e c h nik a l ò s k a | T w o r z y w o | M a s a Nie d o t y c z y
R y s o w a  | M a ciej M a l c z y k

Z a t wie r d zi

P o d zia  k a 1 : 4 | N a z w a p r z e d mio t u Y | | | N r r y s u n k u

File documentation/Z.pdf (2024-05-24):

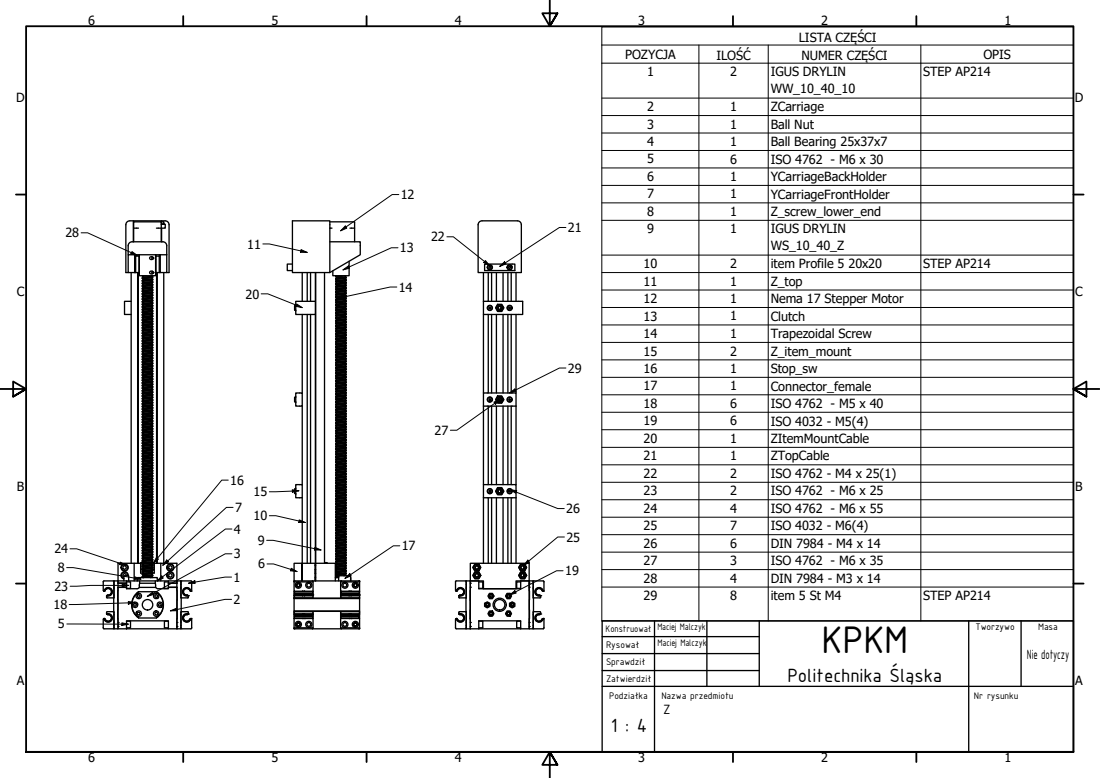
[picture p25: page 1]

P O Z Y C J A |  û I L O |  N U M E R C Z  C I | O P I S
1 | 2 | I G U S D RY L I N W W_ 1 0 _ 4 0 _ 1 0 | S T E P A P 2 1 4

2 | 1 | Z C a r r i a g e
3 | 1 | B all N u t
4 | 1 | B all B e a r i n g 2 5 x 3 7 x 7
5 | 6 | I S O 4 7 6 2 -M 6 x 3 0
6 | 1 | Y C a r r i a g e B a c k H old e r
7 | 1 | Y C a r r i a g e F r o n t H old e r
8 | 1 | Z _ s c r e w _lo w e r_ e n d
9 | 1 | I G U S D RY L I N W S _ 1 0 _ 4 0 _ Z

1 0 | 2 | i t e m P r o f ile 5 2 0 x 2 0 | S T E P A P 2 1 4
1 1 | 1 | Z _t o p
1 2 | 1 | N e m a 1 7 S t e p p e r M o t o r
1 3 | 1 | Clu t c h
1 4 | 1 | T r a p e z o i d al S c r e w
1 5 | 2 | Z _ i t e m _ m o u n t
1 6 | 1 | S t o p _ s w
1 7 | 1 | C o n n e c t o r _fe m ale
1 8 | 6 | I S O 4 7 6 2 -M 5 x 4 0
1 9 | 6 | I S O 4 0 3 2 -M 5 ( 4 )
2 0 | 1 | Z I t e m M o u n t C a ble
2 1 | 1 | Z T o p C a ble
2 2 | 2 | I S O 4 7 6 2 -M 4 x 2 5 ( 1 )
2 3 | 2 | I S O 4 7 6 2 -M 6 x 2 5
2 4 | 4 | I S O 4 7 6 2 -M 6 x 5 5
2 5 | 7 | I S O 4 0 3 2 -M 6 ( 4 )
2 6 | 6 | D I N 7 9 8 4 -M 4 x 1 4
2 7 | 3 | I S O 4 7 6 2 -M 6 x 3 5
2 8 | 4 | D I N 7 9 8 4 -M 3 x 1 4
2 9 | 8 | i t e m 5 S t M 4 | S T E P A P 2 1 4
K o n s t r u o w a  | M a ciej M a l c z y k | | K P K M  P o lit e c h nik a l ò s k a | T w o r z y w o | M a s a Nie d o t y c z y
R y s o w a  | M a ciej M a l c z y k

Z a t wie r d zi

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

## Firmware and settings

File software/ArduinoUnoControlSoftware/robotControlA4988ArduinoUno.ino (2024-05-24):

//Robot control software
//Version for A4988 drivers and STM32 Blue Pill Development board

//screw thread 10mm; motor 200 steps

#include <AccelStepper.h>
#include <ArduinoJson.h>

StaticJsonDocument<40> doc;


//Pin and variable definitions
int ENABLE = 4;
int MS1 = 3;
int MS2 = 2;
int MS3 = 1;
unsigned int pos[3] = {0,0,0};
int spd[3] = {400,1000,400};
String axis[3] = {"x","z","y"};
int end_stop[3] = {7, 6, 5};

//Software reset funcion
void(* resetF) (void) = 0;

//AccelStepper(DRIVER, stepPin, dirPin)
//Speed = step/s; move = step


AccelStepper stepper_matrix[3] = {AccelStepper(1, 13, 12), AccelStepper(1, 11, 10), AccelStepper(1, 9, 8)};

//Motor move funtion definition
void motorMove() {
  String motors_position = "{ \"x\": "+String(stepper_matrix[0].currentPosition(), DEC)+", \"z\": "+String(stepper_matrix[1].currentPosition(), DEC)+", \"y\": "+String(stepper_matrix[2].currentPosition(), DEC)+"}";
  Serial.println(motors_position);
  delay(2); //temporary but works very well
  if (Serial.available() > 0) {
    String line = Serial.readStringUntil('#');
    if (line.length() > 6 & line.length() < 37) {
      DeserializationError error = deserializeJson(doc, line);
      //if json object is malformed print error
      if (error) {
        Serial.print(F("deserializeJson() failed: "));
        Serial.println(error.f_str());
        Serial.println(line);
        return;
      } else {
        if (doc["home"] == 1) {
          resetF();
        } else {
          for (int i=0; i<3; i++) {
            pos[i] = doc[axis[i]];
          }
        }
      }
    } else {
      return;
    }
  } else {
  //set future motor position and enable move to this position
    for(int i=0; i<3; i++) {
      stepper_matrix[i].moveTo(pos[i]);
      stepper_matrix[i].setSpeed(spd[i]);
      stepper_matrix[i].runSpeedToPosition();
    }
  }
}
//zero out axes
void motorsZero() {
  for (int i=0; i<3; i++) {
    stepper_matrix[i].setMaxSpeed(1000);
    stepper_matrix[i].setSpeed(-1000);
    while(true) {
      stepper_matrix[i].runSpeed();
      if (digitalRead(end_stop[i]) == true) {
        stepper_matrix[i].setCurrentPosition(0);
        break;
      }
    }
    Serial.println(i);
  }
}

void setup() {

  //Serial setup. serial timeout set to minimum to avoid problems in movement
  Serial.begin(2000000);
  //Serial.setTimeout(1/(pow(10,10)));
  Serial.setTimeout(5);
  //set modes to pins. This configures micro step mode. Setup for A4988
  pinMode(MS1, OUTPUT);
  pinMode(MS2, OUTPUT);
  pinMode(MS3, OUTPUT);
  pinMode(ENABLE, OUTPUT);

  //HALF STEP
  digitalWrite(ENABLE, LOW);
  digitalWrite(MS1, HIGH);
  digitalWrite(MS2, LOW);
  digitalWrite(MS3, LOW);

  //zero out axes before main loop
  motorsZero();
}


void loop() {
  motorMove();
}
